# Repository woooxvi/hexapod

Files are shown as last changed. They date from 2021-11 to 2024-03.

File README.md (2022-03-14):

#  Hexapod

A Hexapod Robot using Raspberry Pi Zero W

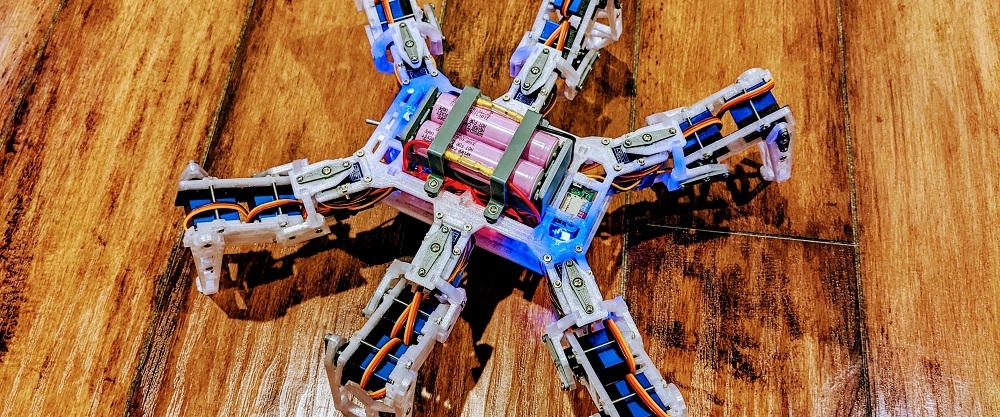
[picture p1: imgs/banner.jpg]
banner


[google_play](https://play.google.com/store/apps/details?id=com.rookiedev.hexapod)
[windows](https://github.com/rookiepeng/hexapod/releases)
[linux](https://github.com/rookiepeng/hexapod/releases)

## Introduction

This is a hexapod robot based on [Smallp Tsai](https://github.com/SmallpTsai)'s [hexapod-v2-7697](https://github.com/SmallpTsai/hexapod-v2-7697) project.
This project reused most of the mechanical design in the original project, but with a full redesign of the circuits and software.
The table below shows the difference between this project and the original one.

| | Original hexapod-v2-7697 | This project |
| --- | --- | --- |
| Controller | Linkit 7697 | Raspberry Pi Zero W or Raspberry Pi Zero W 2 |
| PWM control | Custom circuit board | 2 x PCA9685 motor driver boards |
| DC-DC | 7 x mini360 modules | 2 x XL4005 5A Max DC-DC modules and 1 x mini360 |
| Power | 2S Lipo battery | 2 x 18650 batteries |
| Remote | BLE | WiFi, Bluetooth |
| Remote software | Android and iOS | PC, Android |

https://user-images.githubusercontent.com/471808/148647807-02e3e901-6181-4473-8ac4-3b5998fa8d17.mp4

https://user-images.githubusercontent.com/471808/158099495-1caeb903-a2e6-4e8d-9f13-54728d7d255a.mp4

## Software

### Raspberry Pi

#### Requirements

Raspberry Pi is running [`Raspberry Pi OS`](https://www.raspberrypi.com/software/).

- Enable `I2C` through `raspi-config`

``` bash
sudo raspi-config
```

- Install required packages

``` bash
sudo apt-get install python3-numpy python3-pip
```

- Install required Python modules

``` bash
pip3 install adafruit-circuitpython-servokit
```

> Tips: It is convenient to debug code on Raspberry Pi through VSCode's remote feature.

#### Running

The hexapod program, located under `./software/raspberry pi/`, is written in Python. Use the following command to start it manually.

``` bash
python3 hexapod.py
```

### Android

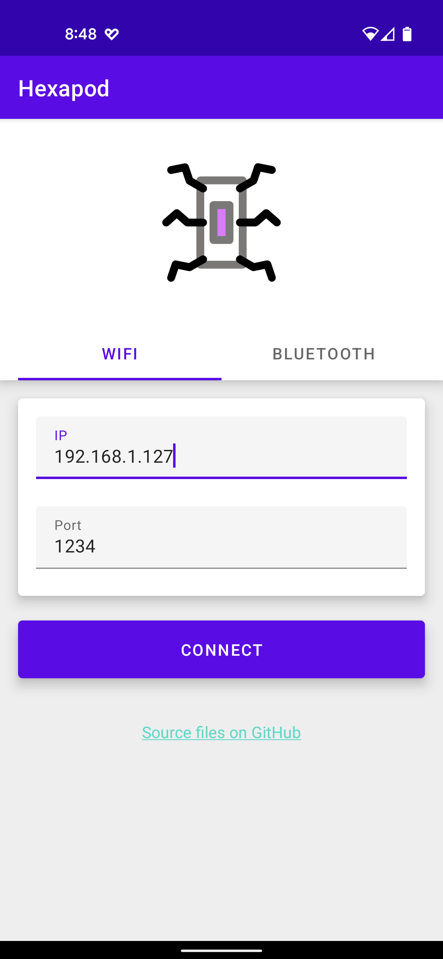
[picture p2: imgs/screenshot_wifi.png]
screenshot_wifi
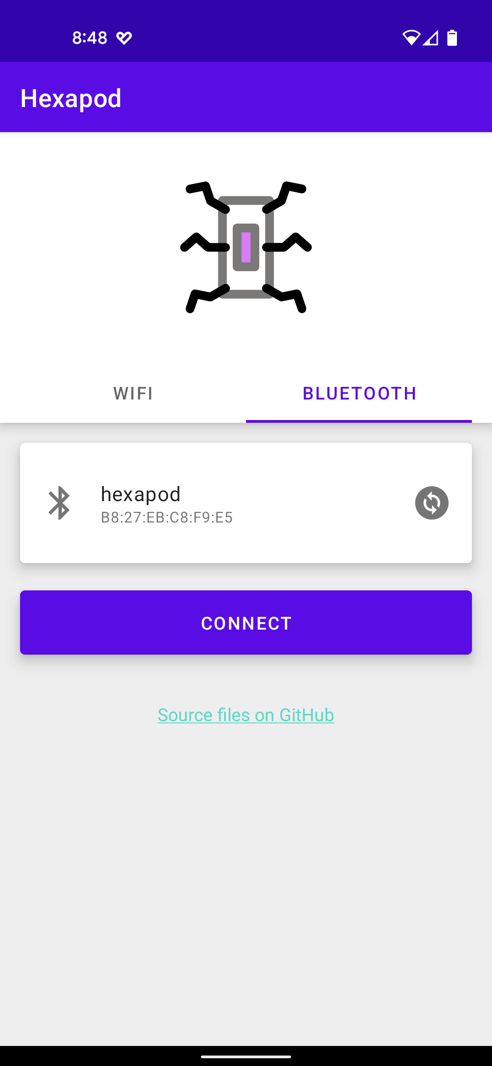
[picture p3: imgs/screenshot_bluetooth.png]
screenshot_bluetooth
 

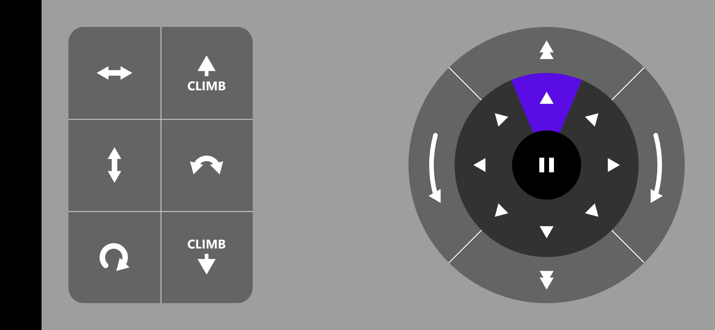
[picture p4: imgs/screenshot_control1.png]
screenshot_control1


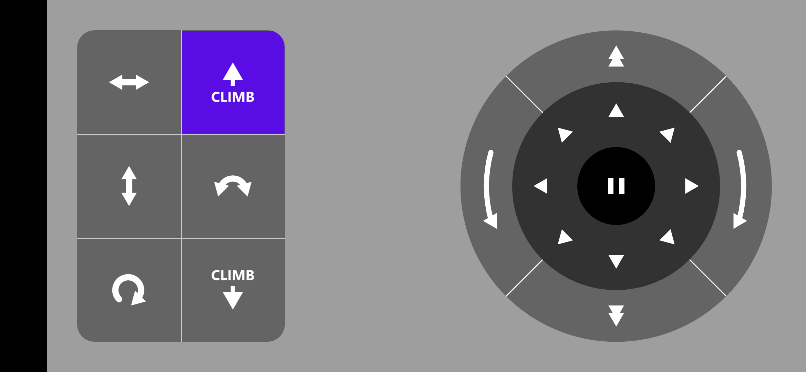
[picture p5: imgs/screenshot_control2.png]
screenshot_control2


### PC

PC program source files are located under `./software/pc/`. The compiled program can be downloaded under the [release](https://github.com/rookiepeng/hexapod/releases) page.

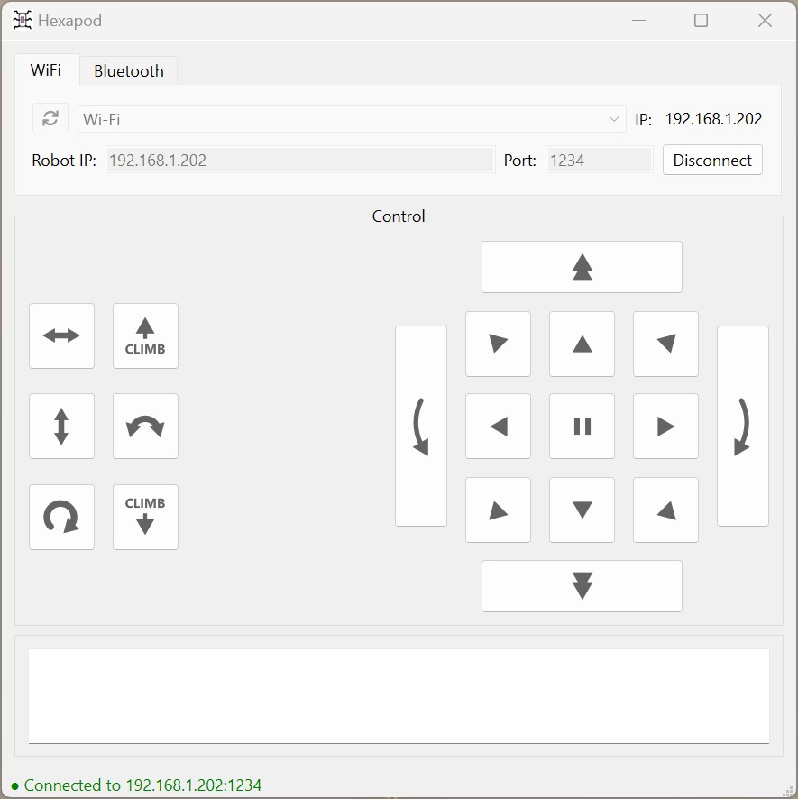
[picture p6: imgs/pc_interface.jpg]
pc_interface


- Find the correct IP address of the Raspberry Pi on the hexapod
- Connect to the hexapod using the IP address
- Use the buttons on the panel to control the hexapod

## Mechanism

### Bill of Materials (BOM)

#### Servos

18 TowerPro [MG92B](http://www.towerpro.com.tw/product/mg92b/) are required.

> The dimension of 3d printed part is highly dependent on the servo's size. Modification is required if you want to use alternative servos.

#### 3D-Printed Parts

##### Body x 1

| Filename | Thumbnail | Required |
| --- | --- | --- |
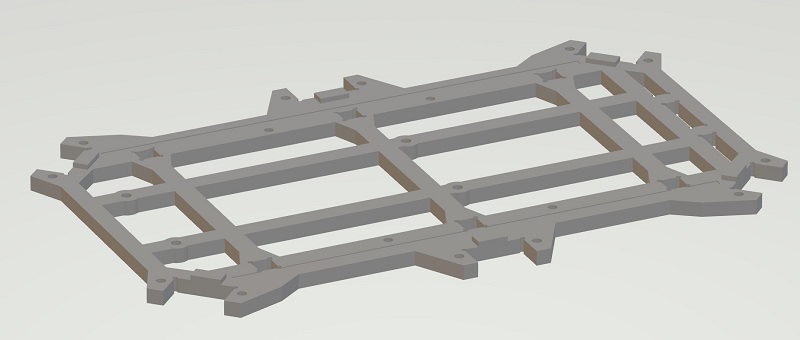
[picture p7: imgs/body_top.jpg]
body_top
| body_top |  | 1 |
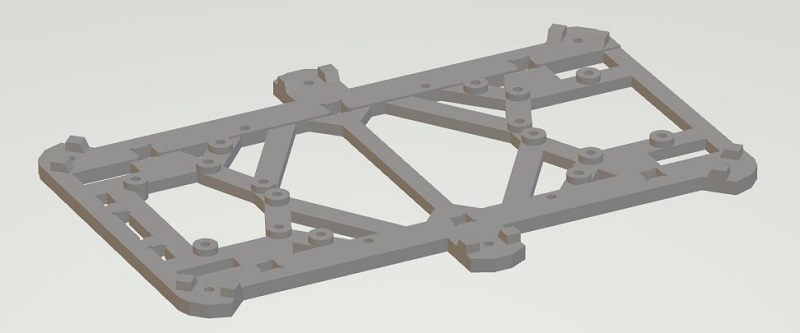
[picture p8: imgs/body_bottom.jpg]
body_bottom
| body_bottom |  | 1 |
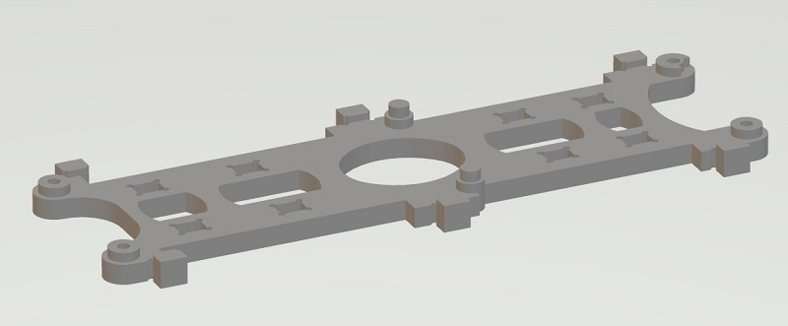
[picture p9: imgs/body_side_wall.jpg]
body_side_wall
| body_side_wall |  | 2 |
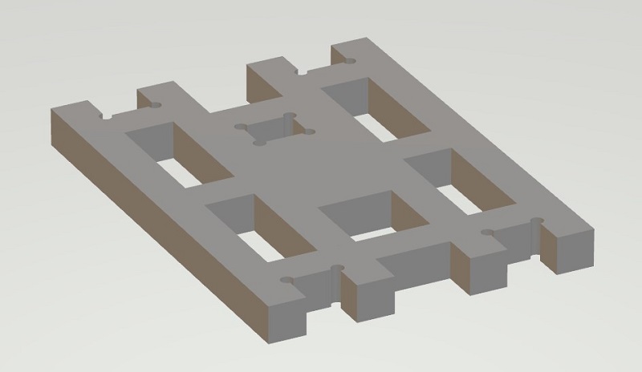
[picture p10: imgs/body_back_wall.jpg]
body_back_wall
| body_back_wall |  | 1 |
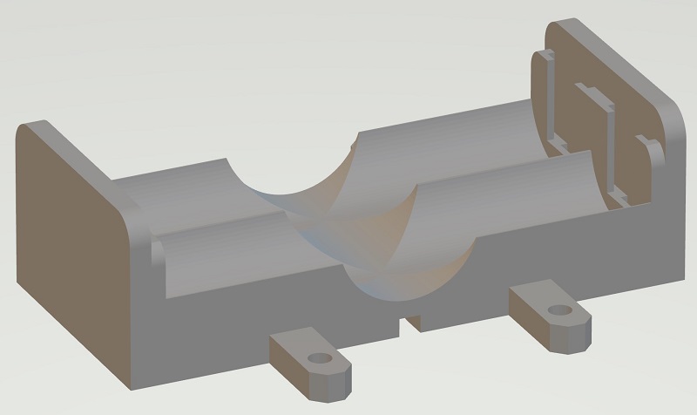
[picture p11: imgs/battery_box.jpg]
battery_box
| battery_box |  | 1 |
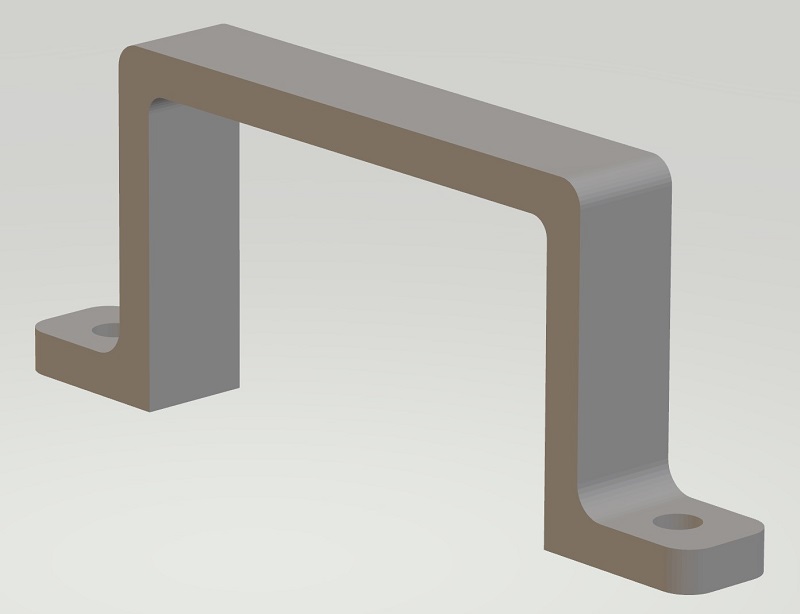
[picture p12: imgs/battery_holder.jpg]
battery_holder
| battery_holder |  | 2 |

##### Leg x 6

| Filename | Thumbnail | Required |
| --- | --- | --- |
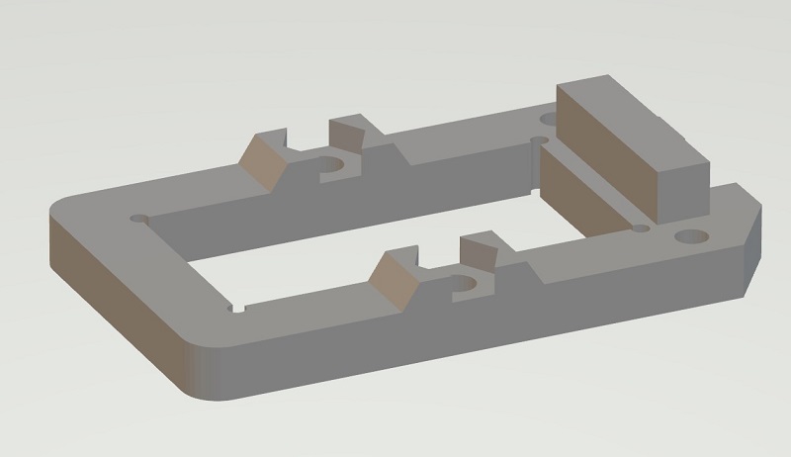
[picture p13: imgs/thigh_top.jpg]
thigh_top
| thigh_top |  | 1 (x6) |
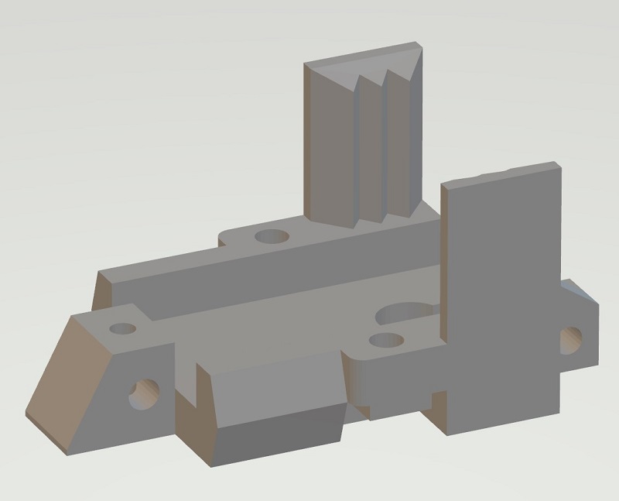
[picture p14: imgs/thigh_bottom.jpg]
thigh_bottom
| thigh_bottom |  | 1 (x6) |
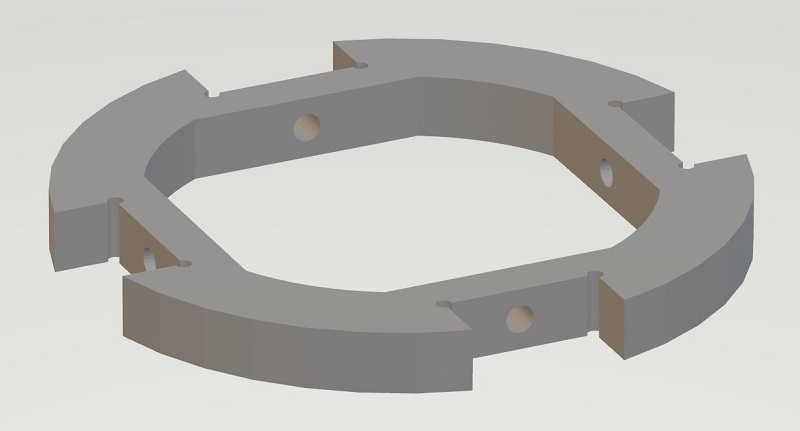
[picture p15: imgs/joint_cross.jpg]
joint_cross
| joint_cross |  | 1 (x6) |
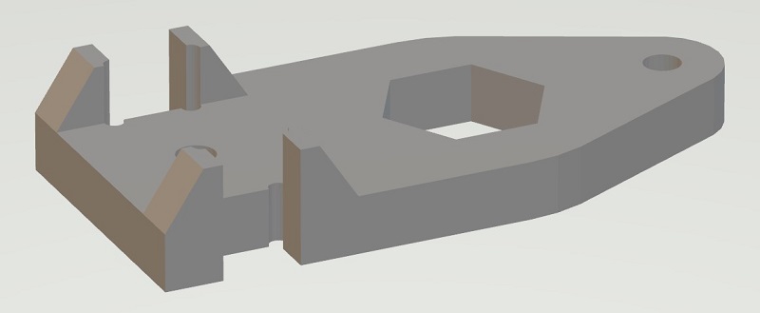
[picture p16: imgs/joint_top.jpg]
joint_top
| joint_top |  | 2 (x6) |
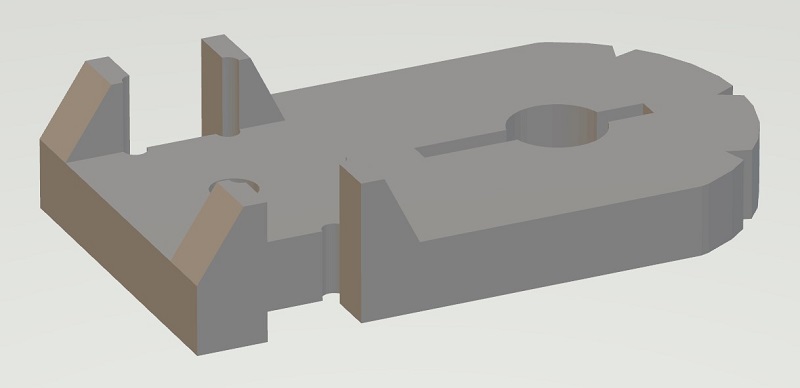
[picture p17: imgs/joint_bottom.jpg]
joint_bottom
| joint_bottom |  | 2 (x6) |
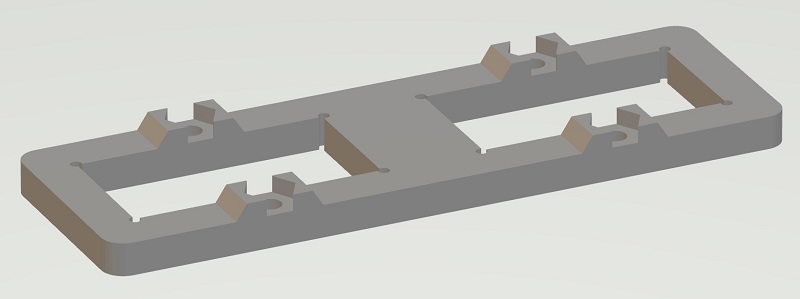
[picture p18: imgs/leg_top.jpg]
leg_top
| leg_top |  | 1 (x6) |
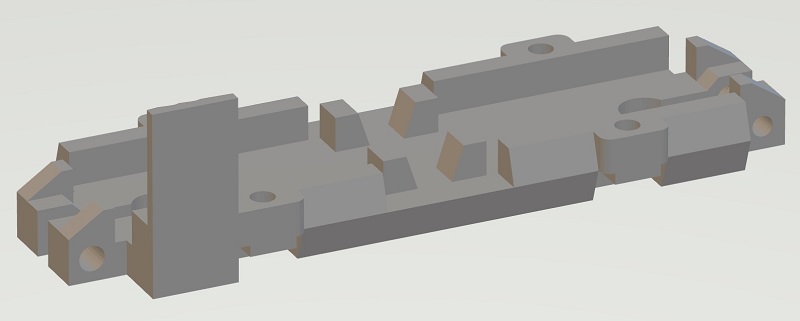
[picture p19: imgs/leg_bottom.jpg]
leg_bottom
| let_bottom |  | 1 (x6) |
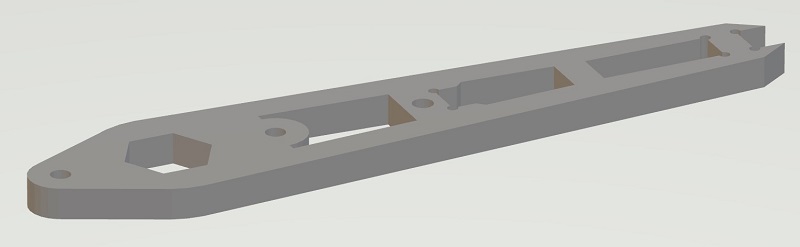
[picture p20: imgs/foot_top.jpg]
foot_top
| foot_top |  | 1 (x6) |
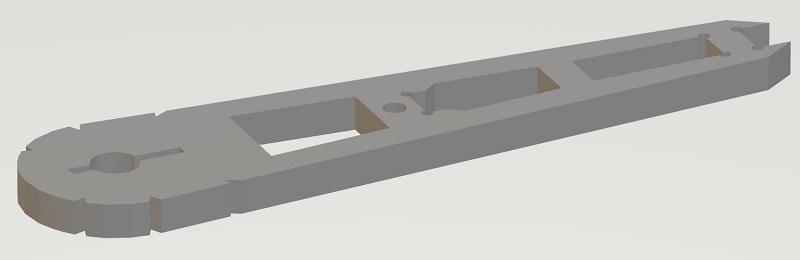
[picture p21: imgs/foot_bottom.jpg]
foot_bottom
| foot_bottom |  | 1 (x6) |
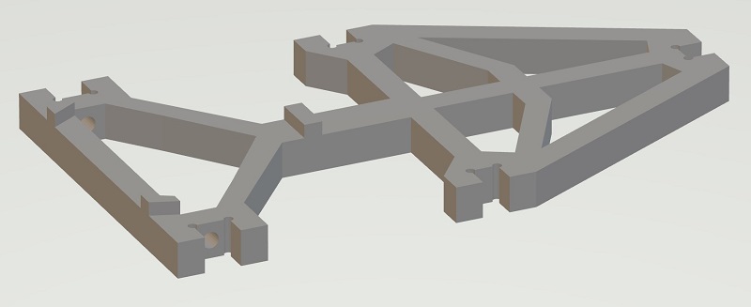
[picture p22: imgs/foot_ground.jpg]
foot_ground
| foot_ground |  | 1 (x6) |
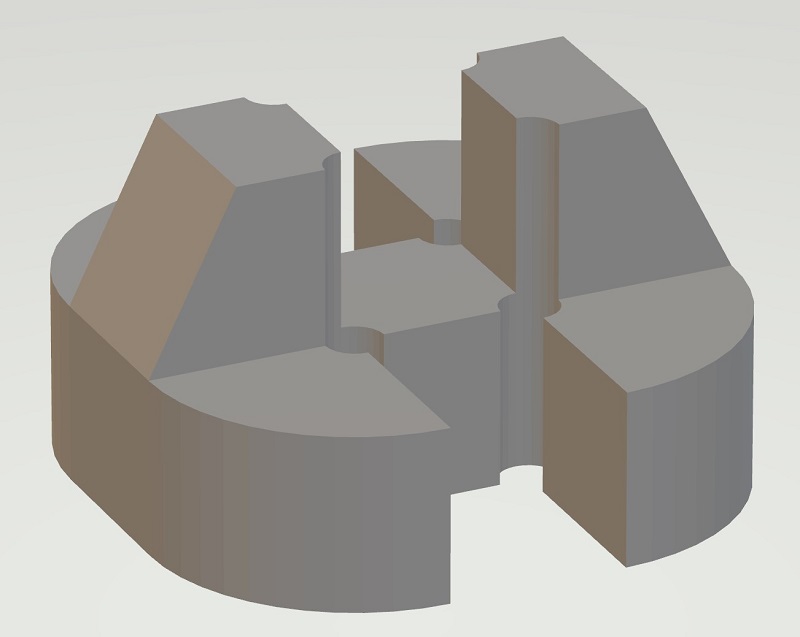
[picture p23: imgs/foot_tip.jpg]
foot_tip
| foot_tip |  | 1 (x6) |
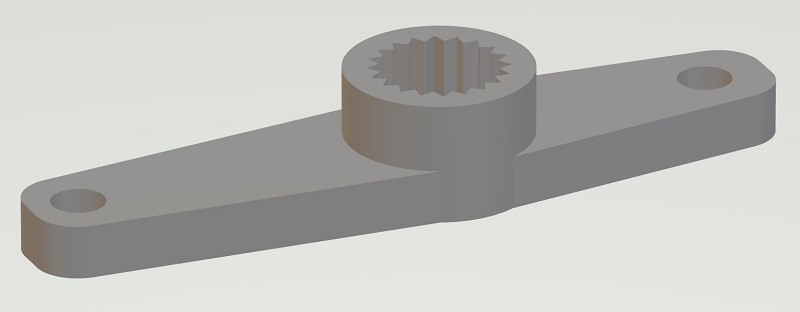
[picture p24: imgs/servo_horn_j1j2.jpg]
servo_horn_j1j2
| servo_horn_j1j2 |  | 2 (x6) |
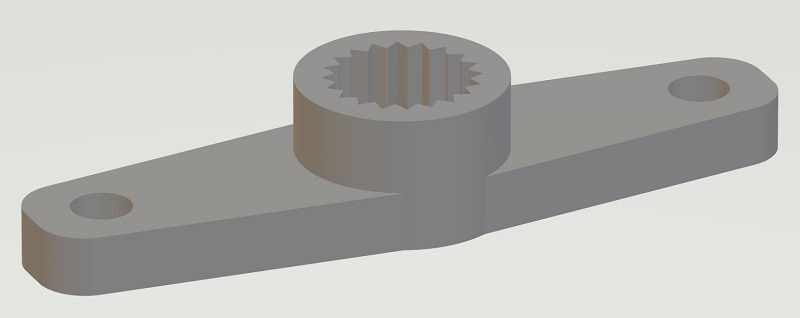
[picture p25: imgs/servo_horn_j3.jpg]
servo_horn_j3
| servo_horn_j3 |  | 1 (x6) |

#### Others

| Name | Spec | Thumbnail | Required | Note |
| --- | --- | --- | --- | --- |
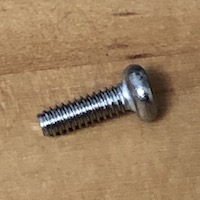
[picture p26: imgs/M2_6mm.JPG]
| Screw | M2 6mm  |  | 54 | Servo Arm: 1 x 18<br>Joint: 4 x 6<br>Thigh: 2 x 6 |
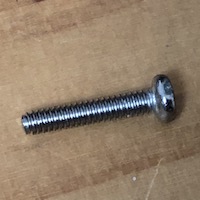
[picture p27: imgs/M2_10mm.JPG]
10mm
| Screw | M2 10mm |  | 24 | Thigh: 1 x 6<br>Pin lock: 1 x 18 |
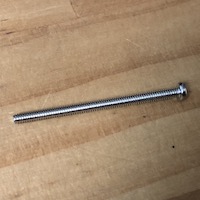
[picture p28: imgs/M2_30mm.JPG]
30mm
| Screw | M2 30mm |  | 36 | Servo: 2 x 18 |
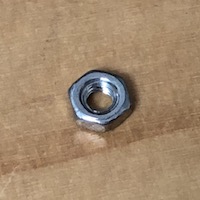
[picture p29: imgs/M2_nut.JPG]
| Nuts | M2 |  | 36 | Servo: 2 x 18 |
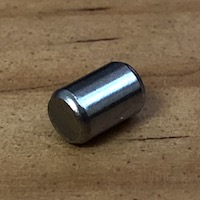
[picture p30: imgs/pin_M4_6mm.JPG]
pin
| Pin (304) | M4 6mm  |  | 18 | Servo: 1 x 18 |

### Leg Assemble

#### Assembly video



#### Exploded view

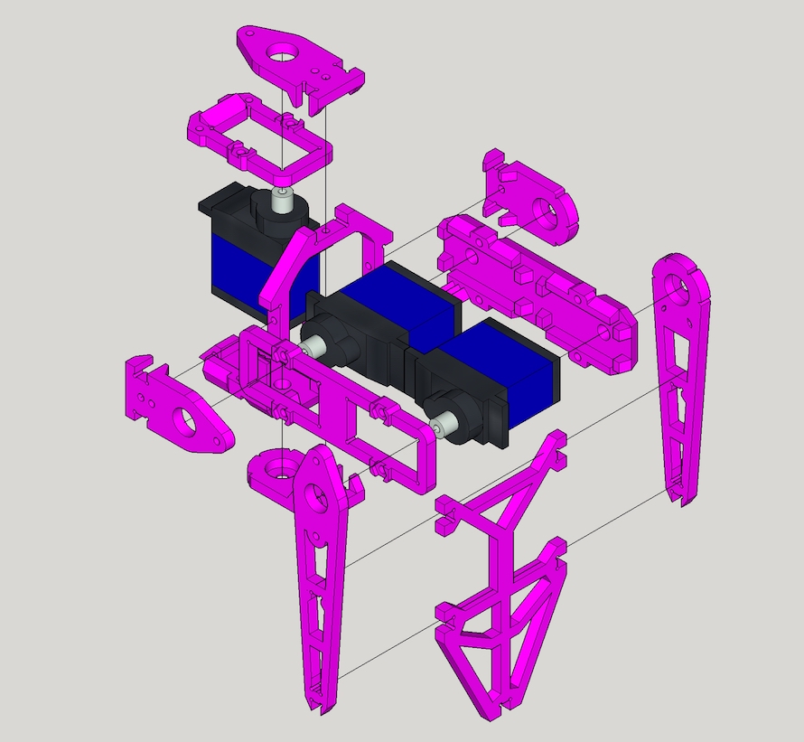
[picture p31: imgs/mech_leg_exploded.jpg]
LegAssemble


#### Detailed steps

- **Step 1** - Combine `thigh_top`, `MG92B` and `thigh_bottom`, use M2x30mm screw and nut to secure them together.

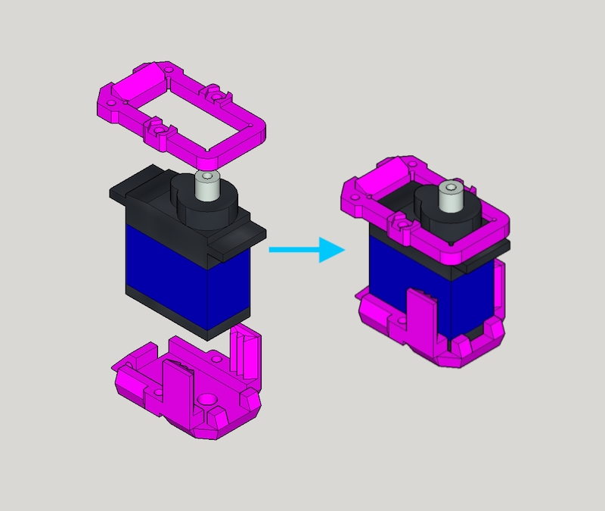
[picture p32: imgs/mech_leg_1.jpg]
LegAssemble1


- **Step 2** - Grab one `joint_cross`, `joint_top` and `joint_bottom` and combine them

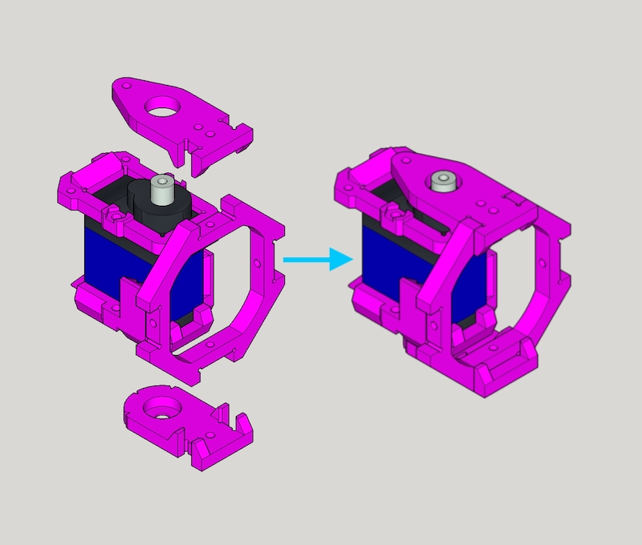
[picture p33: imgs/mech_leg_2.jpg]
LegAssemble2


- **Step 3** - First put 2 x `MG92B`, `leg_top` and `leg_bottom` together with M2x30mm screw and nut. Then attach `joint_top` and `joint_bottom` altogether

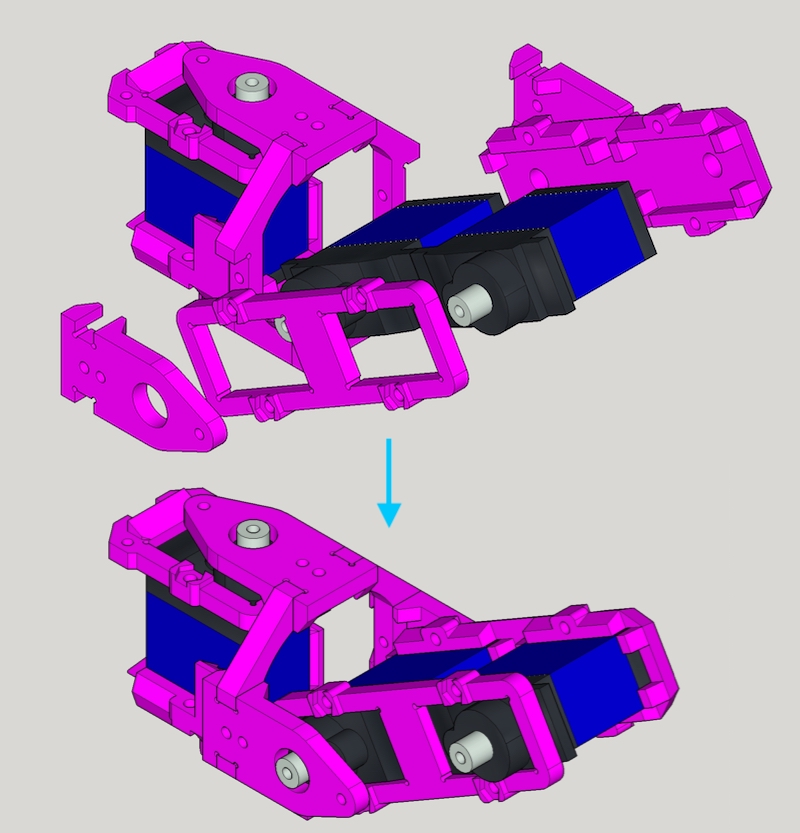
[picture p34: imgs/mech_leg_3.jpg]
LegAssemble3


- **Step 4** - Grab `foot_top`, `foot_bottom` and `foot_ground` (and `foot_top`) and assemble them.

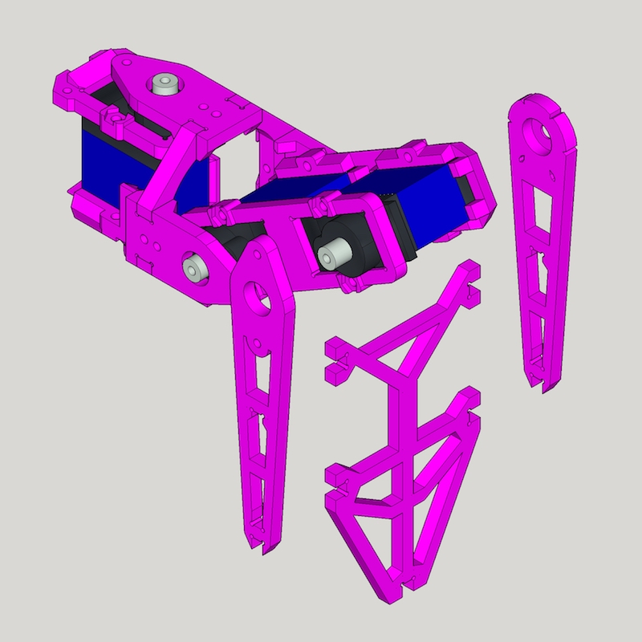
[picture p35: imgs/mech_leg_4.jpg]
LegAssemble4


- **Finish** - Great, you got 1 leg done, 5 more to go :)

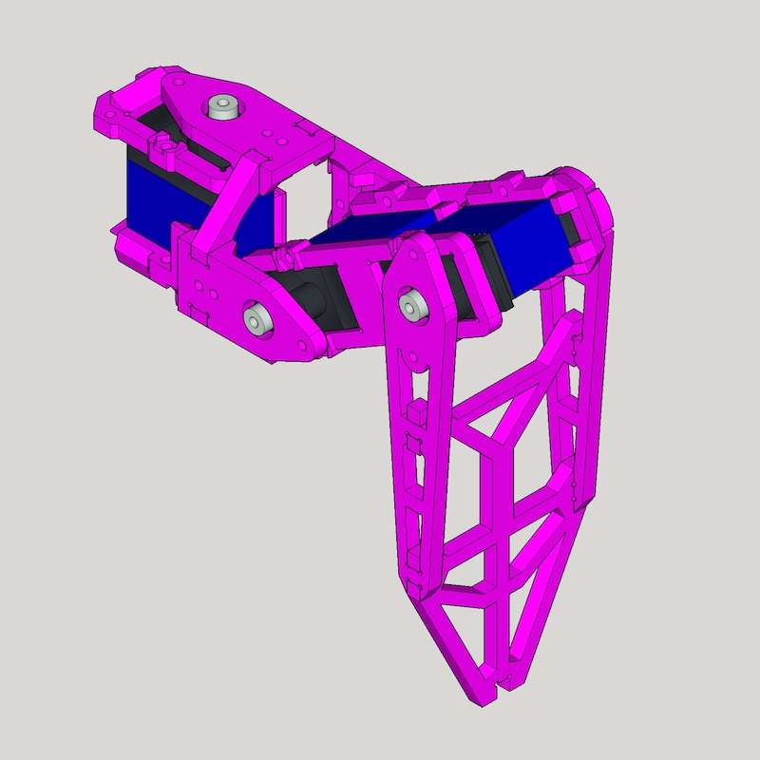
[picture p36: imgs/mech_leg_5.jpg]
LegAssemble5


## Electronics

### Bill of Materials (BOM)

| Name | Thumbnail | Required |
| --- | --- | --- |
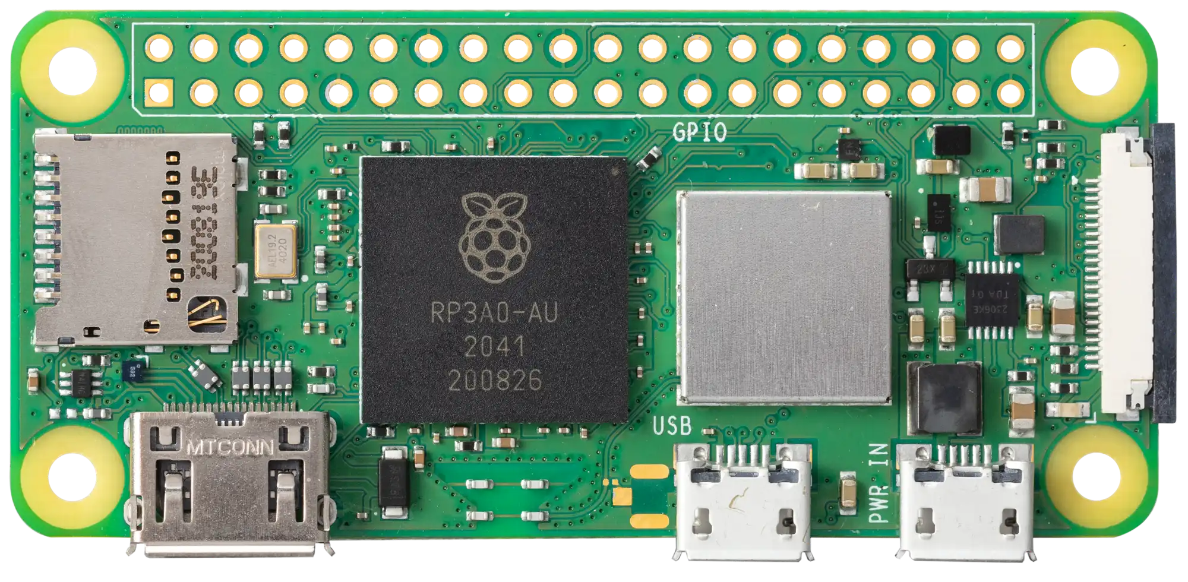
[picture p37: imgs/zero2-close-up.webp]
raspberry pi
| Raspberry Pi Zero W or W 2 |  | 1 |
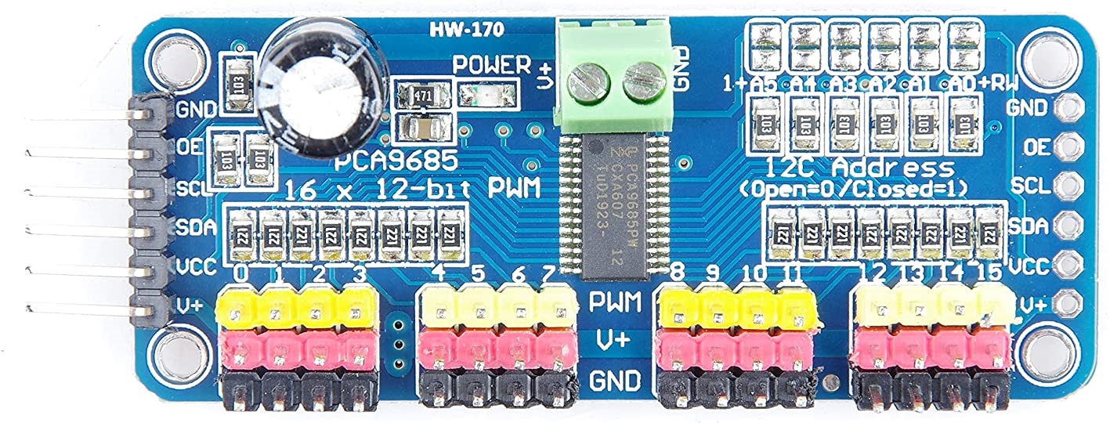
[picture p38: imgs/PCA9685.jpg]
PCA9685
| PCA9685 motor driver |  | 2 |
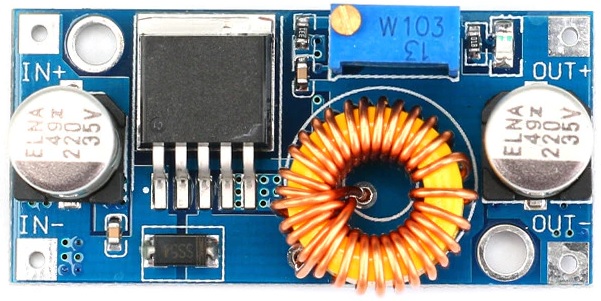
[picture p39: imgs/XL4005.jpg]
XL4005
| XL4005 DC-DC step down |  | 2 |
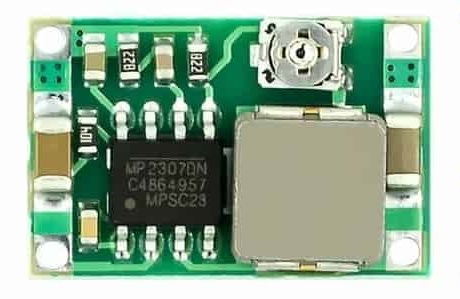
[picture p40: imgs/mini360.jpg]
mini360
| Mini 360 DC-DC step down |  | 1 |
| Toggle switch | toggle_switch  | 1 |

### Connection Diagram

diagram

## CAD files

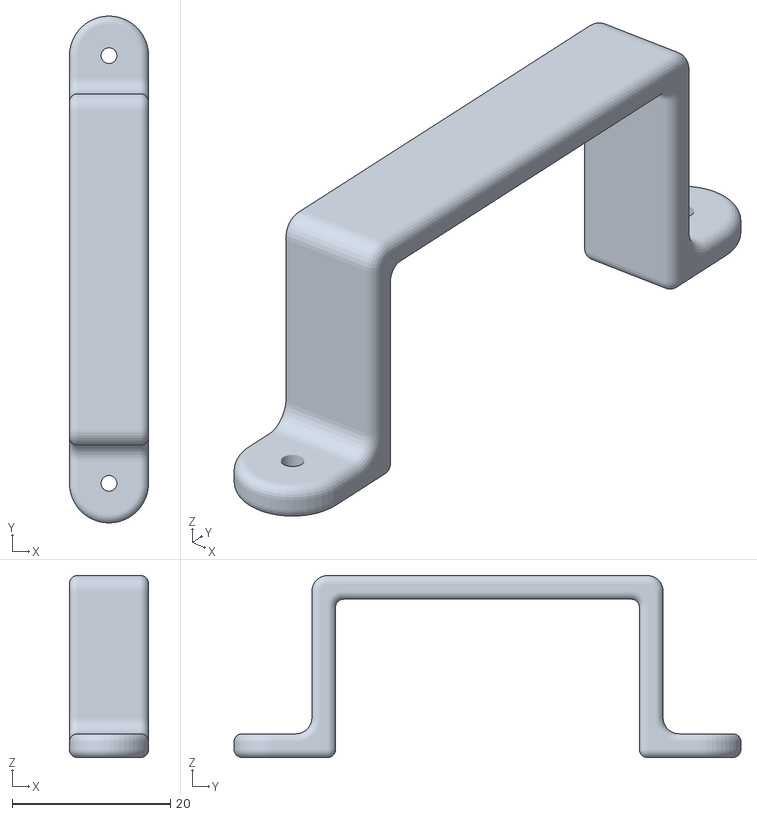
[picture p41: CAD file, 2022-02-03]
mechanism/battery_box_locker.stl
10.0 x 64.1 x 23.0

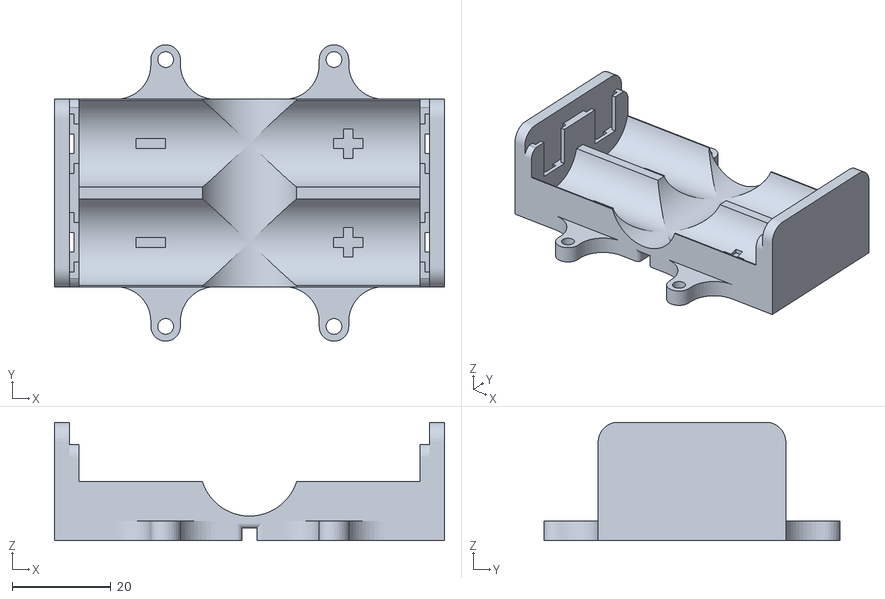
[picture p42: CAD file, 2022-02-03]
mechanism/battery_box.stl
79.0 x 60.1 x 24.0

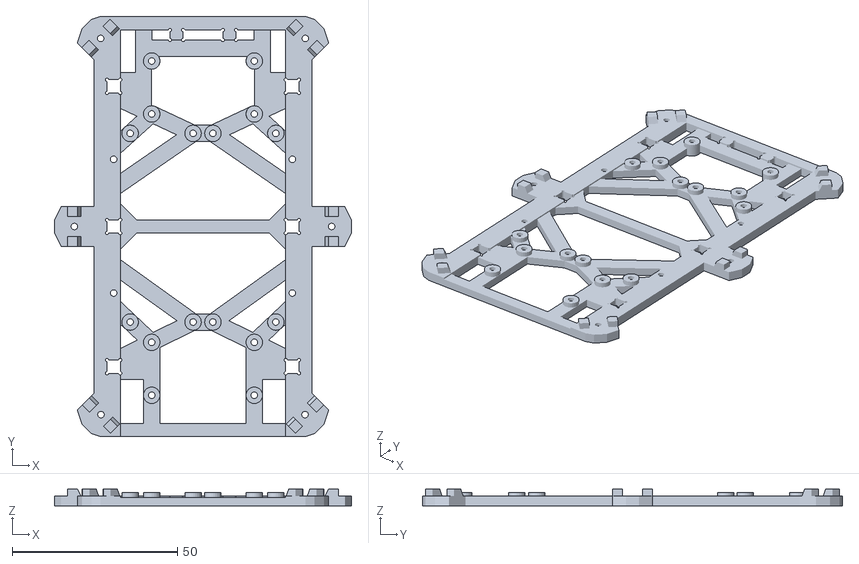
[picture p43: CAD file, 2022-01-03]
mechanism/body_bottom.stl
89.7 x 127.0 x 5.00

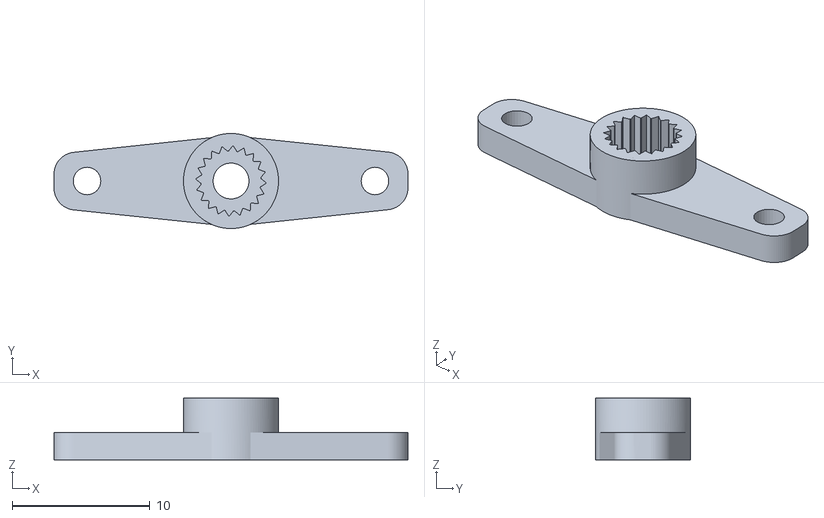
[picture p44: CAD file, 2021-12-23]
mechanism/servo_horn_j3.stl
25.7 x 6.90 x 4.50

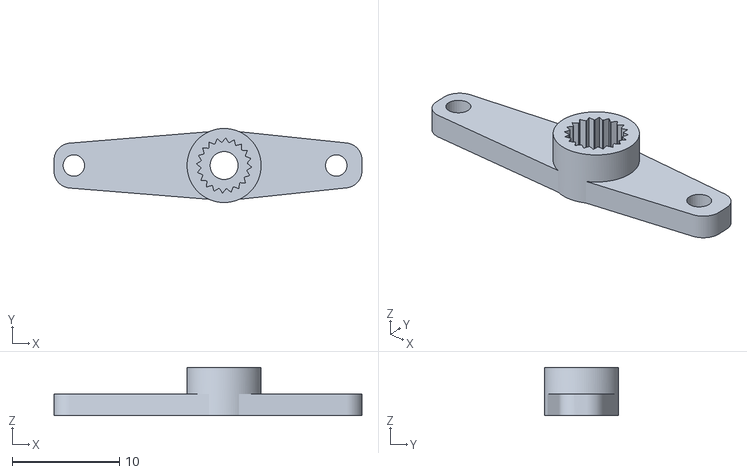
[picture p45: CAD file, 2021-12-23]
mechanism/servo_horn_j1j2.stl
28.7 x 6.90 x 4.50

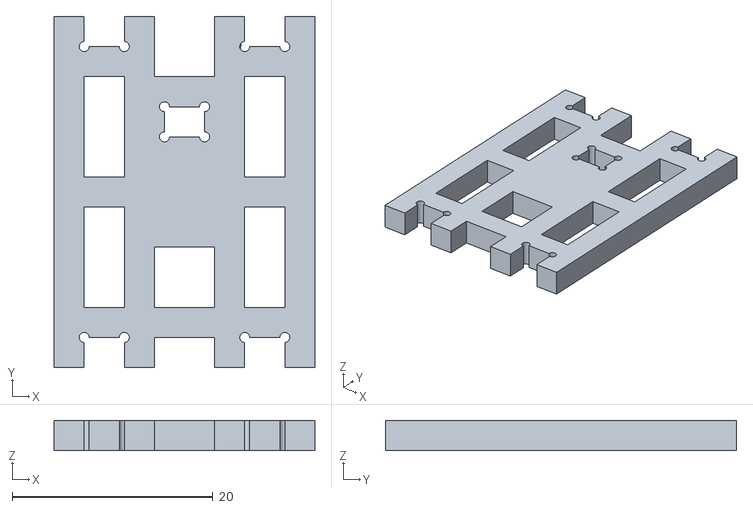
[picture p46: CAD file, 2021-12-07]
mechanism/body_back_wall.stl
26.0 x 35.0 x 3.00

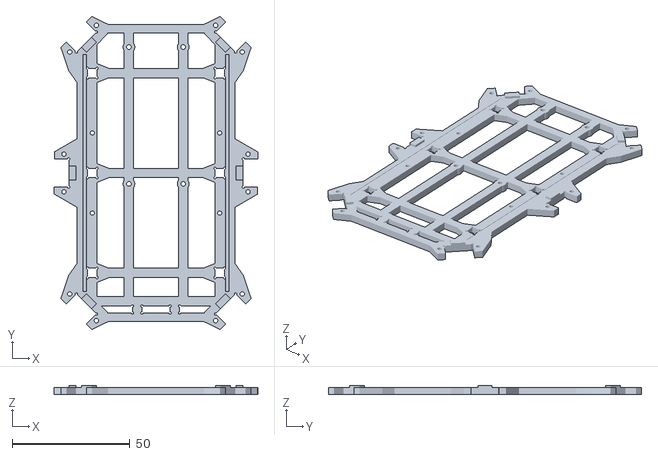
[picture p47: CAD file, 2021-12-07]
mechanism/body_top.stl
86.3 x 132.7 x 4.00

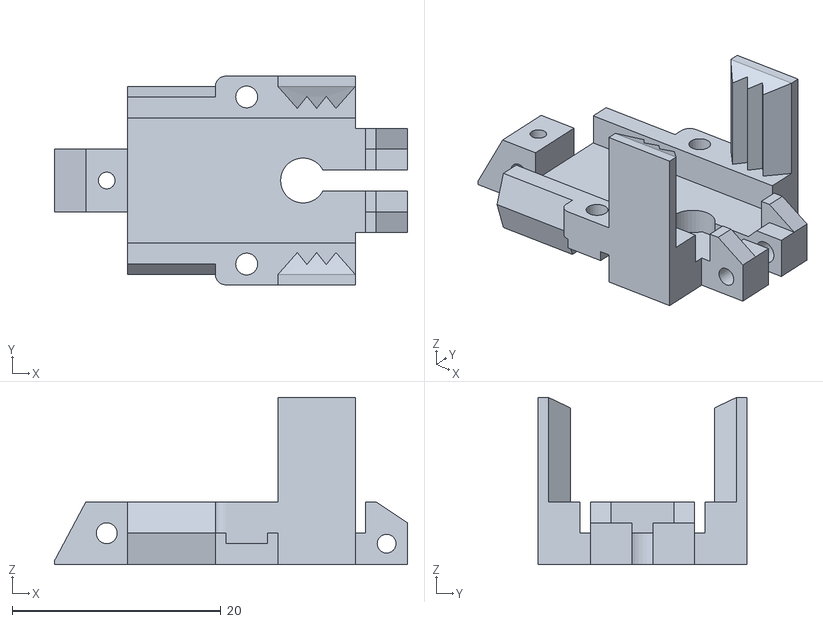
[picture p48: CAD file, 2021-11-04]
mechanism/thigh_bottom.stl
33.8 x 20.0 x 16.0

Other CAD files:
mechanism/Fusion360/body_back_wall.f3d
mechanism/Fusion360/body_bottom.f3d
mechanism/Fusion360/body_top.f3d
mechanism/Fusion360/servo_horn_j1j2.f3d
mechanism/Fusion360/servo_horn_j3.f3d
mechanism/blend files/battery_box.blend
mechanism/blend files/battery_holder.blend

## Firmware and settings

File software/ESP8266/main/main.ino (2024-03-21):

#include <ESP8266WiFi.h>
#include <ArduinoJson.h>
#include <ESP8266WebServer.h>
#include <Adafruit_PWMServoDriver.h>
#include <LinkedList.h>
#include <Ticker.h>


const String ssid = "www.xiaoqiumi.com";
const String passwd = "18648801440";

// const String ssid = "Leray24";
// const String passwd = "leray0410";

const uint8_t MAX_STEP = 10;
uint8_t FRAME_RATE = 15;
const uint8_t LEG_COUNT = 6;
const uint8_t JOINT_COUNT = 3;

Ticker myTicker;

int tickerTotal = 0;

String httpCommand = "";
String postureCommand = "";


ESP8266WebServer server;

Adafruit_PWMServoDriver pwm_l = Adafruit_PWMServoDriver(0x40);
Adafruit_PWMServoDriver pwm_r = Adafruit_PWMServoDriver(0x41);
#define MIN_PULSE_WIDTH 500
#define MAX_PULSE_WIDTH 2500
#define FREQUENCY 50

struct Leg {
  // uint8_t board;
  Adafruit_PWMServoDriver* pwm;
  uint8_t port;
  // float angle;
  float offset;
  // bool reverse;
};

const Leg legs[LEG_COUNT][JOINT_COUNT] = {
  {
    //右前  0
    { &pwm_r, 15, 0.0 },
    { &pwm_r, 14, 0.0 },
    { &pwm_r, 13, 0.0 },
  },
  {
    //右中  1
    { &pwm_r, 12, 0.0 },
    { &pwm_r, 11, 0.0 },
    { &pwm_r, 10, 0.0 },
  },
  {
    //右后  2
    { &pwm_r, 9, 0.0 },
    { &pwm_r, 8, 0.0 },
    { &pwm_r, 7, 0.0 },
  },
  {
    //左后  3
    { &pwm_l, 6, 0.0 },   //坏了？
    { &pwm_l, 7, 0.0 },
    { &pwm_l, 8, 0.0 },   //坏了？
  },
  {
    //左中  4
    { &pwm_l, 3, 0.0 },
    { &pwm_l, 4, 0.0 },
    { &pwm_l, 5, 0.0 },
  },
  {
    //左前  5
    { &pwm_l, 0, 0.0 },
    { &pwm_l, 1, 0.0 },
    { &pwm_l, 2, 0.0 },
  },
}; 

float legStatus[LEG_COUNT][JOINT_COUNT] = {
  {90, 90, 90},
  {90, 90, 90},
  {90, 90, 90},
  {90, 90, 90},
  {90, 90, 90},
  {90, 90, 90},
};

struct Step {
  uint8_t posture[LEG_COUNT][JOINT_COUNT];
  uint16_t elapsed;
};

const Step CMD_forward[MAX_STEP] = {
  { {{131, 137, 54}, {90, 133, 63}, {94, 48, 118}, {90, 144, 63}, {97, 134, 44}, {90, 124, 45}}, 1500 },
  { {{121, 127, 64}, {80, 123, 73}, {84, 58, 118}, {100, 134, 73}, {87, 124, 54}, {80, 114, 55}}, 1500 },
  { {{111, 117, 74}, {70, 113, 83}, {74, 68, 118}, {110, 124, 83}, {77, 114, 64}, {70, 104, 65}}, 1500 },
  { {{121, 127, 64}, {80, 123, 73}, {84, 58, 118}, {100, 134, 73}, {87, 124, 54}, {80, 114, 55}}, 1500 },
  { { {90, 90, 90}, {90, 90, 90}, {90, 90, 90}, {90, 90, 90}, {90, 90, 90}, {90, 90, 90} }, 0 },
  { { {90, 90, 90}, {90, 90, 90}, {90, 90, 90}, {90, 90, 90}, {90, 90, 90}, {90, 90, 90} }, 1000 },
  { { {90, 90, 90}, {90, 90, 90}, {90, 90, 90}, {90, 90, 90}, {90, 90, 90}, {90, 90, 90} }, 1000 },
  { { {90, 90, 90}, {90, 90, 90}, {90, 90, 90}, {90, 90, 90}, {90, 90, 90}, {90, 90, 90} }, 1000 },
  { { {90, 90, 90}, {90, 90, 90}, {90, 90, 90}, {90, 90, 90}, {90, 90, 90}, {90, 90, 90} }, 1000 },
  { { {90, 90, 90}, {90, 90, 90}, {90, 90, 90}, {90, 90, 90}, {90, 90, 90}, {90, 90, 90} }, 1000 },
};

const Step CMD_back[MAX_STEP] = {
  { { {90, 90, 90}, {90, 90, 90}, {90, 90, 90}, {90, 90, 90}, {90, 90, 90}, {90, 90, 90} }, 1000 },
  { { {90, 90, 90}, {90, 90, 90}, {90, 90, 90}, {90, 90, 90}, {90, 90, 90}, {90, 90, 90} }, 1000 },
  { { {90, 90, 90}, {90, 90, 90}, {90, 90, 90}, {90, 90, 90}, {90, 90, 90}, {90, 90, 90} }, 1000 },
  { { {90, 90, 90}, {90, 90, 90}, {90, 90, 90}, {90, 90, 90}, {90, 90, 90}, {90, 90, 90} }, 1000 },
  { { {90, 90, 90}, {90, 90, 90}, {90, 90, 90}, {90, 90, 90}, {90, 90, 90}, {90, 90, 90} }, 1000 },
  { { {90, 90, 90}, {90, 90, 90}, {90, 90, 90}, {90, 90, 90}, {90, 90, 90}, {90, 90, 90} }, 1000 },
  { { {90, 90, 90}, {90, 90, 90}, {90, 90, 90}, {90, 90, 90}, {90, 90, 90}, {90, 90, 90} }, 0 },
  { { {90, 90, 90}, {90, 90, 90}, {90, 90, 90}, {90, 90, 90}, {90, 90, 90}, {90, 90, 90} }, 1000 },
  { { {90, 90, 90}, {90, 90, 90}, {90, 90, 90}, {90, 90, 90}, {90, 90, 90}, {90, 90, 90} }, 1000 },
  { { {90, 90, 90}, {90, 90, 90}, {90, 90, 90}, {90, 90, 90}, {90, 90, 90}, {90, 90, 90} }, 1000 },
};

const Step CMD_left[MAX_STEP] = {
  { { {90, 90, 90}, {90, 90, 90}, {90, 90, 90}, {90, 90, 90}, {90, 90, 90}, {90, 90, 90} }, 1000 },
  { { {90, 90, 90}, {90, 90, 90}, {90, 90, 90}, {90, 90, 90}, {90, 90, 90}, {90, 90, 90} }, 1000 },
  { { {90, 90, 90}, {90, 90, 90}, {90, 90, 90}, {90, 90, 90}, {90, 90, 90}, {90, 90, 90} }, 1000 },
  { { {90, 90, 90}, {90, 90, 90}, {90, 90, 90}, {90, 90, 90}, {90, 90, 90}, {90, 90, 90} }, 1000 },
  { { {90, 90, 90}, {90, 90, 90}, {90, 90, 90}, {90, 90, 90}, {90, 90, 90}, {90, 90, 90} }, 1000 },
  { { {90, 90, 90}, {90, 90, 90}, {90, 90, 90}, {90, 90, 90}, {90, 90, 90}, {90, 90, 90} }, 0 },
  { { {90, 90, 90}, {90, 90, 90}, {90, 90, 90}, {90, 90, 90}, {90, 90, 90}, {90, 90, 90} }, 1000 },
  { { {90, 90, 90}, {90, 90, 90}, {90, 90, 90}, {90, 90, 90}, {90, 90, 90}, {90, 90, 90} }, 1000 },
  { { {90, 90, 90}, {90, 90, 90}, {90, 90, 90}, {90, 90, 90}, {90, 90, 90}, {90, 90, 90} }, 1000 },
  { { {90, 90, 90}, {90, 90, 90}, {90, 90, 90}, {90, 90, 90}, {90, 90, 90}, {90, 90, 90} }, 1000 },
};

const Step CMD_right[MAX_STEP] = {
  { { {90, 90, 90}, {90, 90, 90}, {90, 90, 90}, {90, 90, 90}, {90, 90, 90}, {90, 90, 90} }, 1000 },
  { { {90, 90, 90}, {90, 90, 90}, {90, 90, 90}, {90, 90, 90}, {90, 90, 90}, {90, 90, 90} }, 1000 },
  { { {90, 90, 90}, {90, 90, 90}, {90, 90, 90}, {90, 90, 90}, {90, 90, 90}, {90, 90, 90} }, 1000 },
  { { {90, 90, 90}, {90, 90, 90}, {90, 90, 90}, {90, 90, 90}, {90, 90, 90}, {90, 90, 90} }, 1000 },
  { { {90, 90, 90}, {90, 90, 90}, {90, 90, 90}, {90, 90, 90}, {90, 90, 90}, {90, 90, 90} }, 1000 },
  { { {90, 90, 90}, {90, 90, 90}, {90, 90, 90}, {90, 90, 90}, {90, 90, 90}, {90, 90, 90} }, 1000 },
  { { {90, 90, 90}, {90, 90, 90}, {90, 90, 90}, {90, 90, 90}, {90, 90, 90}, {90, 90, 90} }, 1000 },
  { { {90, 90, 90}, {90, 90, 90}, {90, 90, 90}, {90, 90, 90}, {90, 90, 90}, {90, 90, 90} }, 1000 },
  { { {90, 90, 90}, {90, 90, 90}, {90, 90, 90}, {90, 90, 90}, {90, 90, 90}, {90, 90, 90} }, 1000 },
  { { {90, 90, 90}, {90, 90, 90}, {90, 90, 90}, {90, 90, 90}, {90, 90, 90}, {90, 90, 90} }, 0 },
};

Step currStep = { { {90, 90, 90}, {90, 90, 90}, {90, 90, 90}, {90, 90, 90}, {90, 90, 90}, {90, 90, 90} }, 0 };

//                      首步首循  首步骤首循后  首步n循后 首步N0循后 二步首循前   二步首循后  二步n循后 二步N1循后  执行完M步后首次循环前
//------------------------------------------------------------------------------------------------------------------------------------
// currStepIdx        | 0         0             0         0      →  1             1         1         1           0
// currStepFrameIdx   | 0         1             n         N0     →  0             1         n         N1          0
// currStepFrameCount | 0    →    N0            N0        N0     →  0     →       N1        N1        N1          N0
// cmdRound           | 0         0             0         0      →  1             1         1         1           M

const Step* currTask;
// Step const (*currTask)[MAX_STEP] = NULL;
uint8_t currTaskStepCount = 0;

uint8_t currStepIdx = 0;
uint8_t currStepFrameIdx = 0;
uint8_t currStepFrameCount = 0;
int cmdRound = 0;
uint16_t elapsedPreadd = 2000;

//减速
float taskSacle = 1.0;
uint8_t printTaskLevel = 0;

void setup() {
  Serial.println("Enter setup");
  // put your setup code here, to run once:
  Serial.begin(115200);
  pinMode(0, INPUT);
  pinMode(LED_BUILTIN, OUTPUT);

  // setupPWM();
  pwm_l.begin();
  pwm_r.begin();
  pwm_l.setPWMFreq(FREQUENCY);  // Analog servos run at ~50 Hz updates
  pwm_r.setPWMFreq(FREQUENCY);  // Analog servos run at ~50 Hz updates

  // setupWifi();
  // 设置WiFi运行模式为无线终端模式
  WiFi.mode(WIFI_STA);
  // // 为当前设备配置固定IP
  // if (!WiFi.config(host, gateway, netmask)) {
  //   Serial.println("Can't config wifi.");
  // }
  Serial.println("Connecting to " + ssid);
  // 连接WiFi
  WiFi.begin(ssid, passwd);
  // 判断是否连接成功
  while (WiFi.status() != WL_CONNECTED) {
    Serial.print('.');
    delay(100);
  }
  Serial.println("");
  Serial.println("Connected to " + ssid);

  // setupWS();
  server.onNotFound(httpCommandHandler);
  server.begin(80);
  Serial.println("HTTP server started");

  myTicker.attach_ms(1000 / FRAME_RATE, moveFrame);

  delay(1000);
  
  Serial.print("Current ip address is ");
  Serial.println(WiFi.localIP());

}


void moveFrame(){
  tickerTotal++;
  if(currTask != NULL || currStep.elapsed != 0){
    if(currTask != NULL){
      currStep.elapsed = currTask[currStepIdx].elapsed;
      for(int legIdx = 0; legIdx < LEG_COUNT; legIdx++) {
        for(int jointIdx = 0; jointIdx < JOINT_COUNT; jointIdx++) {
          currStep.posture[legIdx][jointIdx] = currTask[currStepIdx].posture[legIdx][jointIdx];
        }
      }
    }
    if(currStepFrameIdx==0){
      Serial.print("=================进入步骤, cmdRound=");
      Serial.print(cmdRound);
      Serial.print(", currStepIdx=");
      Serial.print(currStepIdx);
      // Serial.print(", currStepFrameIdx=");
      // Serial.print(currStepFrameIdx);

      Serial.print(" elapsed=(");
      Serial.print(currStep.elapsed);

      uint16_t elapsed = currStep.elapsed;
        //首次进入加多三秒
      if(cmdRound==0) { 
        Serial.print("+");
        Serial.print(elapsedPreadd);
        elapsed += elapsedPreadd;
      }
      elapsed *= taskSacle;
      Serial.print(")*");
      Serial.print(taskSacle);
      Serial.print(" = ");
      Serial.print(elapsed);

      //计算需要的步骤数 currStepFrameCount == 0
      currStepFrameCount = ceil(elapsed / 1000.0 * FRAME_RATE);
      Serial.print(", currStepFrameCount=");
      Serial.print(currStepFrameCount);

    }
    // float legStatusPrev[LEG_COUNT][JOINT_COUNT];   ); Serial.print(
    uint8_t currStepFrameLess = currStepFrameCount-currStepFrameIdx;
    if(printTaskLevel==0) {
      Serial.println("");
      Serial.print("执行Step:"); Serial.print(currStepIdx); Serial.print(", Frame:"); Serial.print(currStepFrameIdx); Serial.print("/"); Serial.print(currStepFrameCount); Serial.print(", cmdRound:"); Serial.print(cmdRound);
    }

    for(int legIdx = 0; legIdx < LEG_COUNT; legIdx++) {
      if(printTaskLevel==0 || currStepFrameIdx==0) Serial.print("\n");
      for(int jointIdx = 0; jointIdx < JOINT_COUNT; jointIdx++) {
        float angleLess = currStep.posture[legIdx][jointIdx] - legStatus[legIdx][jointIdx];
        float angleLessStep = angleLess / currStepFrameLess;
        float targetAngle = legStatus[legIdx][jointIdx] + angleLessStep;
        // legStatusPrev[legIdx][jointIdx] = legStatus[legIdx][jointIdx];
        float prevAngle = exeServoMotor(legIdx, jointIdx, targetAngle, true, true, false);
        if(printTaskLevel==0){
          if(prevAngle >= 0){
            Serial.print(formatFloat(prevAngle)); Serial.print(" + "); Serial.print(formatFloat(angleLessStep)); Serial.print(" → "); Serial.print(formatFloat(targetAngle)); Serial.print(", ");
          }else{
            Serial.print(formatFloat(legStatus[legIdx][jointIdx])); Serial.print(" + "); Serial.print(formatFloat(angleLessStep)); Serial.print(" → error, ");
          }
        }else if(currStepFrameIdx==0){
          Serial.print(formatFloat(prevAngle)); Serial.print(" + "); Serial.print(formatFloat(angleLess)); Serial.print(" → "); Serial.print(formatFloat(currStep.posture[legIdx][jointIdx])); Serial.print(", ");
        }
      }
      // legIdx++;
    }
    currStepFrameIdx++;
    if(printTaskLevel==0 || currStepFrameIdx==currStepFrameCount) Serial.println("");
    else Serial.print(".");
    if(currStepFrameIdx==currStepFrameCount){
      if(currTask == NULL){
        stopTask();
      }else{
        //x步Nx循后
        currStepIdx++;
        currStepFrameIdx=0;
        currStepFrameCount=0;
        cmdRound++;
        if(currStepIdx==currTaskStepCount){
          //下一次循环
          currStepIdx=0;
        }
      }
    }
  }

  
      // uint8_t maxDistance = 0;
      // for(uint8_t stepIdx = 0; stepIdx < sizeof(currTask); stepIdx++){
        

      //   if(stepIdx+1<sizeof(currTask) && currTask[stepIdx].interval == 0) break;
      // }
}


void loop() {
  // int start = tickerTotal;
  String command = Serial.readString();
  if (command != "") {
    Serial.println("");
    Serial.println("got Serial command:" + command);
  }
    // Serial.print("cost time(Serial):");
    // Serial.println((tickerTotal - start) / 10.0);
    // start=tickerTotal;


  if (command == "") {
    server.handleClient();
    command = httpCommand;
    httpCommand = "";
    // Serial.print("cost time(Http):");
    // Serial.println((tickerTotal - start) / 10.0);
    // start=tickerTotal;
    if(command != ""){
      Serial.println("");
      Serial.println("got Http command:" + command);
    }
  }

  if (command == "") {
    command = postureCommand;
    if(command != ""){
      Serial.println("");
      Serial.println("got Posture command:" + command);
    }
  }

  if (command != "") {
    String portStr = command.substring(1, 3);
    String boardStr = command.substring(0, 1);
    String angleStr = command.substring(3);
    Adafruit_PWMServoDriver* pwm;
    if (boardStr == "l") {
      pwm = &pwm_l;
    } else if (boardStr == "r") {
      pwm = &pwm_r;
    } else {
      Serial.print("?");
    }
    int port = portStr.toInt();
    int angle = angleStr.toInt();
    Serial.print("set ");
    Serial.print(boardStr);
    Serial.print(port);
    Serial.print(" to ");
    Serial.println(angle);
    pwm->setPWM(port, 0, pulseWidth(angle));
  }else{
  }
}

void httpCommandHandler() {
  server.sendHeader("Access-Control-Allow-Origin", "*");
  server.sendHeader("Access-Control-Allow-Headers", "Origin, X-Requested-With, Content-Type, Accept");
  String command = server.uri().substring(1);
  String data;
  int len = server.arg(0).length();
  if (len > 0) data = server.arg(0);


  if (command == "yo"){
    server.send(200, "text/plain", "yo");
    Serial.println("新的问候");


  } else if (command == "stop"){
    stopTask();
    server.send(200, "text/plain", command);


  } else if (command =="cmd" || command == "move") {
    bool withFix = (command == "move");
    stopTask();
    JsonDocument doc;
    deserializeJson(doc, data);
    uint8_t legIdx = doc["LegIdx"].as<uint8_t>();
    uint8_t jointIdx = doc["JointIdx"].as<uint8_t>();
    float angle = doc["Angle"].as<float>();
    bool hasErr = false;
    if (legIdx < 0 || legIdx >= LEG_COUNT) {
      Serial.print("illegal legIdx");
      Serial.println(legIdx);
      hasErr = true;
    }
    if (jointIdx < 0 || jointIdx >= JOINT_COUNT) {
      Serial.print("illegal jointIdx");
      Serial.println(jointIdx);
      hasErr = true;
    }
    if(hasErr == false){
      exeServoMotor(legIdx, jointIdx, angle, withFix, true, true);
    }
    server.send(200, "text/plain", data);


  } else if (command =="cmdpos" || command == "movepos") {
    bool withFix = (command == "movepos");
    stopTask();
    // Serial.println(command + ",withFix" + withFix);
    JsonDocument doc;
    deserializeJson(doc, data);
    JsonArray legAngles = doc.as<JsonArray>();

    uint8_t legIdx = 0, jointIdx = 0;
    for(JsonArray legAngle : legAngles){
      jointIdx=0;
      for(JsonVariant jointAngle : legAngle){
        float angle = jointAngle.as<uint8_t>();
        // Serial.print("l:"); Serial.print(legIdx); Serial.print("j:"); Serial.print(jointIdx); Serial.print("angle:"); Serial.println(angle);
        currStep.posture[legIdx][jointIdx] = angle;
        // exeServoMotor(legIdx, jointIdx, angle, withFix, true, true);
        jointIdx++;
      }
      legIdx++;
    }
    currStep.elapsed = 1000;
    startTask(NULL, 0);

    // // Serial.println("read data done:" + data);
    // uint8_t legIdx = 0, jointIdx = 0;
    // for(JsonArray legAngle : legAngles){
    //   jointIdx=0;
    //   for(JsonVariant jointAngle : legAngle){
    //     float angle = jointAngle.as<uint8_t>();
    //     exeServoMotor(legIdx, jointIdx, angle, withFix, true, true);
    //     jointIdx++;
    //   }
    //   legIdx++;
    // }
    Serial.print("legIdx:"); Serial.print(legIdx); Serial.print(", jointIdx:"); Serial.println(jointIdx);
    server.send(200, "text/plain", data);

 
  } else if (command =="setting") {
    JsonDocument doc;
    deserializeJson(doc, data);
    if(doc.containsKey("TaskSacle")) taskSacle = doc["TaskSacle"].as<float>();
    if(doc.containsKey("PrintTaskLevel")) printTaskLevel = doc["PrintTaskLevel"].as<uint8_t>();
    if(doc.containsKey("FrameRate")) FRAME_RATE = doc["FrameRate"].as<uint8_t>();
    server.send(200, "text/plain", data);

  } else if (command.startsWith("task/")) {
    command = command.substring(5);
    const Step* _currTask = NULL;
    if( command == "forward" ){
      _currTask = CMD_forward;
    }else if ( command == "back" ){
      _currTask = CMD_back;
    }else if ( command == "left" ){
      _currTask = CMD_left;
    }else if ( command == "right" ){
      _currTask = CMD_right;
    }
    if(_currTask == NULL){
      server.send(200, "text/plain", "unknow task:" + command);
      Serial.println("unknow task:" + command);
      return;
    }else{ 
      stopTask();
      startTask(_currTask, 2000);
      Serial.println("");
      server.send(200, "text/plain", "into task:" + command + ",stepCount:" + currTaskStepCount);
      Serial.println("into task:" + command);
    }

  }
}

void startTask(const Step* _currTask, uint16_t _elapsedPreadd){
  // 移动？
  // currTask[0].elapsed = 0;
  // for(uint8_t i = 0; i < MAX_STEP; i++){
  //   if(i==0) currTask[i].elapsed = _currTask[i].elapsed;
  //   for(uint8_t legIdx = 0; legIdx < MAX_STEP; legIdx++){
  //     for(uint8_t jointIdx = 0; jointIdx < MAX_STEP; jointIdx++){
  //       currTask[i].posture[legIdx][jointIdx] = _currTask[i].posture[legIdx][jointIdx];
  //     }
  //   }
  // }
  if(_currTask == NULL){
    currTaskStepCount = 1;
  } else {
    for(uint8_t i = 0; i < MAX_STEP; i++){
      if(_currTask[i].elapsed == 0) {
        currTaskStepCount = i;
        break;
      }
    }
  }

  currStepIdx = 0;
  currStepFrameIdx = 0;
  currStepFrameCount = 0;
  cmdRound = 0;
  elapsedPreadd = _elapsedPreadd;
  currTask = _currTask;
  // currTask[i].elapsed = _currTask[i].elapsed;
}

void stopTask(){
  currTask = NULL;
  currStep.elapsed = 0;
  currStepIdx = 0;
  currStepFrameIdx = 0;
  currStepFrameCount = 0;
  cmdRound = 0;
  currTaskStepCount = 0;
  Serial.println("Task Stoped!");
}

//成功返回旧角度，否则返回-1
float exeServoMotor(uint8_t legIdx, uint8_t jointIdx, float angle, bool withFix, bool force, bool log) {
  const Leg* _leg = &legs[legIdx][jointIdx];
  if(log){
    Serial.print("legIdx = ");Serial.print(legIdx);Serial.print(";");
    Serial.print("jointIdx = ");Serial.print(jointIdx);Serial.print(";");
  }
  float angleTruth = angle;
  if ( withFix ) {
    angleTruth = angle + _leg -> offset;
  }
  if (angleTruth < 0 || angleTruth > 180) {
    if(log){
      Serial.print("illegal angle:");
      Serial.print(angleTruth);
      if(angle != angleTruth) Serial.print("["); Serial.print(angle); Serial.print("]");
      Serial.println("");
    }
    return -1;  //illegal angle
  } else if (!force && legStatus[legIdx][jointIdx] == angleTruth) {
    if(log){
      Serial.print("unchange angle:");
      Serial.print(angleTruth);
      if(angle != angleTruth) {Serial.print("["); Serial.print(angle); Serial.print("]");}
      Serial.println("");
    }
    return -2;  //unchange angle
  } else {
    float prevAngle = legStatus[legIdx][jointIdx];
    if(log){
      // 通过串口监视器输出解析后的数据信息
      Serial.print("angleNow = ");Serial.print(prevAngle);Serial.print(";");
      Serial.print(" -> "); Serial.print(angleTruth);
      Serial.println();
    }
    _leg->pwm->setPWM(_leg->port, 0, pulseWidth(angleTruth)); 
    legStatus[legIdx][jointIdx] = angleTruth;
    return prevAngle;
    // pwm.setPWM(1, 0, pulseWidth(180));   // 1号接口输出180度
  }
}

// PWM舵机控制函数
float pulseWidth(float angle) {
  float pulse_wide, analog_value;
  pulse_wide = map(angle, 0, 180, MIN_PULSE_WIDTH, MAX_PULSE_WIDTH);
  analog_value = float(pulse_wide) / 1000000.0 * FREQUENCY * 4096.0;
  return analog_value;
}

String formatFloat(float value){  
    // 确保值不超过128  
    if (value > 128.0) {  
        value = 128.0;  
    }  
  
    // 分离整数部分和小数部分  
    int intPart = static_cast<int>(value);  
    float fracPart = value - intPart;  
  
    // 格式化整数部分，确保有三位数字（前面补0）  
    char intStr[4];  
    snprintf(intStr, sizeof(intStr), "%03d", intPart);  
  
    // 格式化小数部分，保留一位小数（后面补0）  
    char fracStr[3];  
    if (fracPart < 0.1) {  
        strcpy(fracStr, "00"); // 如果小数部分为0，则直接赋值为"00"  
    } else {  
        int roundedFrac = static_cast<int>(round(fracPart * 10)); // 四舍五入到最接近的整数  
        snprintf(fracStr, sizeof(fracStr), "%01d0", roundedFrac); // 转换为字符串，并确保有两位数字（第二位为0）  
    }  
  
    // 合并整数部分和小数部分  
    String result = String(intStr) + "." + String(fracStr[0]); // 注意：这里只取了fracStr的第一位，因为我们已经确保了它只有一位有效数字  
    return result;  
}

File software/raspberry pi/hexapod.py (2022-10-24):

#!python
#
# 2021 - PRESENT  Zhengyu Peng
# Website: https://zpeng.me
#
# `                      `
# -:.                  -#:
# -//:.              -###:
# -////:.          -#####:
# -/:.://:.      -###++##:
# ..   `://:-  -###+. :##:
#        `:/+####+.   :##:
# .::::::::/+###.     :##:
# .////-----+##:    `:###:
#  `-//:.   :##:  `:###/.
#    `-//:. :##:`:###/.
#      `-//:+######/.
#        `-/+####/.
#          `+##+.
#           :##:
#           :##:
#           :##:
#           :##:
#           :##:
#            .+:

# Libraries
# https://circuitpython.readthedocs.io/projects/servokit/en/latest/
from audioop import reverse
from adafruit_servokit import ServoKit

from leg import Leg

from queue import Queue, Empty

# python3-numpy
import numpy as np
import time
import json
from path_generator import gen_walk_path
from path_generator import gen_fastwalk_path
from path_generator import gen_turn_path
# from path_generator import gen_shift_path
from path_generator import gen_climb_path
from path_generator import gen_rotatex_path, gen_rotatey_path, gen_rotatez_path
from path_generator import gen_twist_path

from threading import Thread

from tcpserver import TCPServer
from btserver import BluetoothServer


class Hexapod(Thread):
    CMD_STANDBY = 'standby'
    CMD_LAYDOWN = 'laydown'

    CMD_WALK_0 = 'walk0'
    CMD_WALK_180 = 'walk180'

    CMD_WALK_R45 = 'walkr45'
    CMD_WALK_R90 = 'walkr90'
    CMD_WALK_R135 = 'walkr135'

    CMD_WALK_L45 = 'walkl45'
    CMD_WALK_L90 = 'walkl90'
    CMD_WALK_L135 = 'walkl135'

    CMD_FASTFORWARD = 'fastforward'
    CMD_FASTBACKWARD = 'fastbackward'

    CMD_TURNLEFT = 'turnleft'
    CMD_TURNRIGHT = 'turnright'

    CMD_CLIMBFORWARD = 'climbforward'
    CMD_CLIMBBACKWARD = 'climbbackward'

    CMD_ROTATEX = 'rotatex'
    CMD_ROTATEY = 'rotatey'
    CMD_ROTATEZ = 'rotatez'

    CMD_TWIST = 'twist'

    CMD_CALIBRATION = 'calibration'
    CMD_NORMAL = 'normal'

    def __init__(self, in_cmd_queue):
        Thread.__init__(self)

        self.cmd_queue = in_cmd_queue
        self.interval = 0.005

        self.calibration_mode = False

        with open('/home/pi/hexapod/software/raspberry pi/config.json', 'r') as read_file:
            self.config = json.load(read_file)

        # legs' coordinates
        # x -> right
        # y -> front
        # z -> up
        # origin is the center of the body
        # roots are the positions of the bottom screws
        # length units are in mm
        # time units are in ms
        self.mount_x = np.array(self.config['legMountX'])
        self.mount_y = np.array(self.config['legMountY'])
        self.root_j1 = self.config['legRootToJoint1']
        self.j1_j2 = self.config['legJoint1ToJoint2']
        self.j2_j3 = self.config['legJoint2ToJoint3']
        self.j3_tip = self.config['legJoint3ToTip']
        self.mount_angle = np.array(self.config['legMountAngle'])/180*np.pi
        self.mount_position = np.zeros((6, 3))
        self.mount_position[:, 0] = self.mount_x
        self.mount_position[:, 1] = self.mount_y

        # Objects
        self.pca_right = ServoKit(channels=16, address=0x40, frequency=120)
        self.pca_left = ServoKit(channels=16, address=0x41, frequency=120)

        self.legs = [
            # front right
            Leg(0,
                [self.pca_left.servo[13], self.pca_left.servo[14],
                 self.pca_left.servo[15]],
                correction=self.config.get('leg0Offset', [0, 0, 0])),
            # center right
            Leg(1,
                [self.pca_left.servo[9], self.pca_left.servo[5],
                 self.pca_left.servo[6]],
                correction=self.config.get('leg1Offset', [0, 0, 0])),
            # rear right
            Leg(2,
                [self.pca_left.servo[3], self.pca_left.servo[0],
                 self.pca_left.servo[1]],
                correction=self.config.get('leg2Offset', [0, 0, 0])),
            # rear left
            Leg(3,
                [self.pca_right.servo[13], self.pca_right.servo[15],
                 self.pca_right.servo[14]],
                correction=self.config.get('leg3Offset', [0, 0, 0])),
            # center left
            Leg(4,
                [self.pca_right.servo[9], self.pca_right.servo[6],
                 self.pca_right.servo[7]],
                correction=self.config.get('leg4Offset', [0, 0, 0])),
            # front left
            Leg(5,
                [self.pca_right.servo[3], self.pca_right.servo[1],
                 self.pca_right.servo[0]],
                correction=self.config.get('leg5Offset', [0, 0, 0]))]

        # self.leg_0.reset(True)
        # self.leg_1.reset(True)
        # self.leg_2.reset(True)
        # self.leg_3.reset(True)
        # self.leg_4.reset(True)
        # self.leg_5.reset(True)

        self.standby_posture = self.gen_posture(60, 75)

        self.current_motion = self.standby_posture

        self.cmd_dict = {
            self.CMD_STANDBY: self.standby_posture,
            self.CMD_LAYDOWN: self.gen_posture(0, 15),
            self.CMD_WALK_0: gen_walk_path(
                self.standby_posture['coord'], direction=0),
            self.CMD_WALK_180: gen_walk_path(
                self.standby_posture['coord'], direction=180),
            self.CMD_WALK_R45: gen_walk_path(
                self.standby_posture['coord'], direction=315),
            self.CMD_WALK_R90: gen_walk_path(
                self.standby_posture['coord'], direction=270),
            self.CMD_WALK_R135: gen_walk_path(
                self.standby_posture['coord'], direction=225),
            self.CMD_WALK_L45: gen_walk_path(
                self.standby_posture['coord'], direction=45),
            self.CMD_WALK_L90: gen_walk_path(
                self.standby_posture['coord'], direction=90),
            self.CMD_WALK_L135: gen_walk_path(
                self.standby_posture['coord'], direction=135),
            self.CMD_FASTFORWARD: gen_fastwalk_path(
                self.standby_posture['coord']),
            self.CMD_FASTBACKWARD: gen_fastwalk_path(
                self.standby_posture['coord'], reverse=True),
            self.CMD_TURNLEFT: gen_turn_path(
                self.standby_posture['coord'], direction='left'),
            self.CMD_TURNRIGHT: gen_turn_path(
                self.standby_posture['coord'], direction='right'),
            self.CMD_CLIMBFORWARD: gen_climb_path(
                self.standby_posture['coord'], reverse=False),
            self.CMD_CLIMBBACKWARD: gen_climb_path(
                self.standby_posture['coord'], reverse=True),
            self.CMD_ROTATEX: gen_rotatex_path(self.standby_posture['coord']),
            self.CMD_ROTATEY: gen_rotatey_path(self.standby_posture['coord']),
            self.CMD_ROTATEZ: gen_rotatez_path(self.standby_posture['coord']),
            self.CMD_TWIST: gen_twist_path(self.standby_posture['coord'])
        }

        self.posture(self.standby_posture['coord'])
        time.sleep(1)
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

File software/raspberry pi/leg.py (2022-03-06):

#!python
#
# 2021  Zhengyu Peng
# Website: https://zpeng.me
#
# `                      `
# -:.                  -#:
# -//:.              -###:
# -////:.          -#####:
# -/:.://:.      -###++##:
# ..   `://:-  -###+. :##:
#        `:/+####+.   :##:
# .::::::::/+###.     :##:
# .////-----+##:    `:###:
#  `-//:.   :##:  `:###/.
#    `-//:. :##:`:###/.
#      `-//:+######/.
#        `-/+####/.
#          `+##+.
#           :##:
#           :##:
#           :##:
#           :##:
#           :##:
#            .+:

import numpy as np


class Leg:
    def __init__(self,
                 id,
                 junction_servos,
                 correction=[0, 0, 0],
                 scale=[1, 1, 1],
                 constraint=[[35, 145], [0, 165], [30, 150]]):
        self.id = id
        self.junction_servos = junction_servos
        self.correction = correction
        self.constraint = constraint

    def set_angle(self, junction, angle):
        set_angle = np.min(
            [angle+self.correction[junction], self.constraint[junction][1]+self.correction[junction], 180])
        set_angle = np.max(
            [set_angle, self.constraint[junction][0]+self.correction[junction], 0])
        self.junction_servos[junction].angle = set_angle

    def set_raw_angle(self, junction, angle):
        self.junction_servos[junction].angle = angle

    def move_junctions(self, angles):
        self.set_angle(0, angles[0])
        self.set_angle(1, angles[1])
        self.set_angle(2, angles[2])

    def reset(self, calibrated=False):
        if calibrated:
            self.set_angle(0, 90)
            self.set_angle(1, 90)
            self.set_angle(2, 90)
        else:
            self.set_raw_angle(0, 90)
            self.set_raw_angle(1, 90)
            self.set_raw_angle(2, 90)

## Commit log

2021-11-04 tweak stl models
    [body_bottom.blend, body_bottom.stl, body_top.blend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]
2021-11-27 add Leg and Hexapod classes
2021-11-30 battery box
    [Battery_box_for_18650_cells.scad, Battery_box_for_18650_cells.stl]
2021-12-06 update design
    [battery_box.blend, body_bottom.blend, body_top.blend]
2021-12-06 update stl
    [battery_box.stl, body_bottom.stl, body_top.stl]
2021-12-07 flip front and back
    [hexapod.py]
2021-12-08 calibrate legs
2021-12-08 update calibration
2021-12-20 add servo horn models
    [servo_horn_j1j2.blend, servo_horn_j1j2.stl, servo_horn_j3.blend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]
2021-12-29 add battery holder
    [battery_holder.blend, battery_holder.stl]
2022-02-03 update battery box stl
    [battery_box.stl, battery_box_locker.stl, battery_holder.stl]
2022-03-06 get calibration data from config
2022-11-02 add dotnet version run on raspberry pi
2022-11-04 make every leg in single thread
